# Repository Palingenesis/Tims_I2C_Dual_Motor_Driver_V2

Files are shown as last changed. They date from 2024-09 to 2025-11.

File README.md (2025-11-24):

# This is My I2C Dual Motor Driver Version 2  
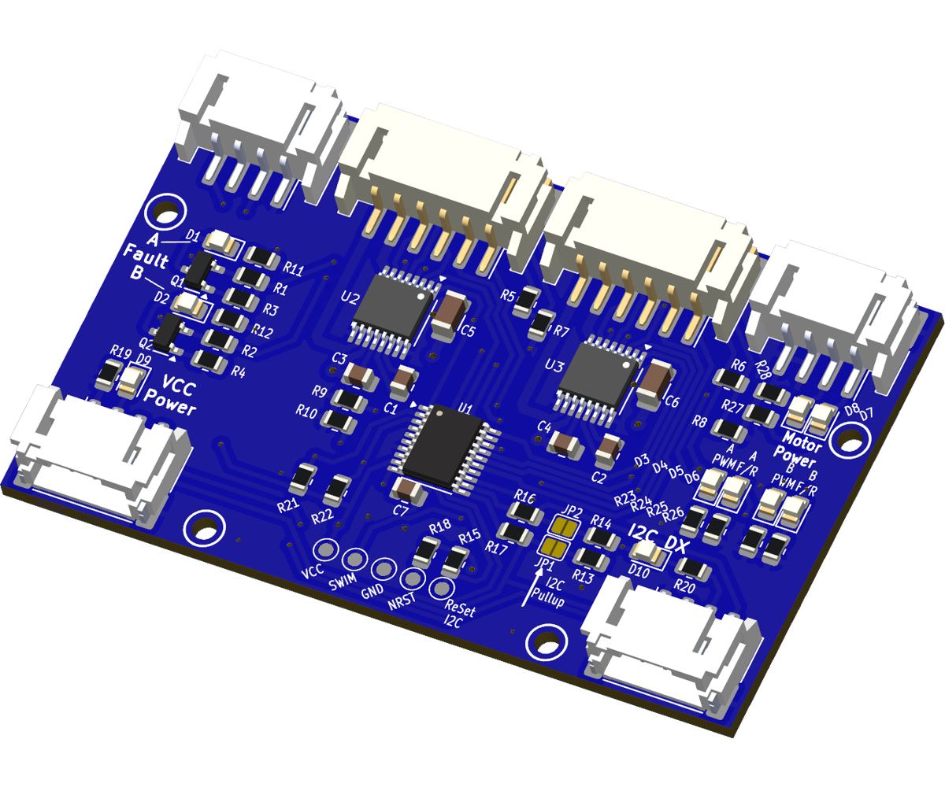
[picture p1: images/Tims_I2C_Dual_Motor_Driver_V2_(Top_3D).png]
3D Top
  
## This is an I2C controlled Dual Motor Driver Board.  
<span style="color: red; font-weight: bold;">This Board supperceeds this one [Tims I2C Dual Motor Driver](https://github.com/Palingenesis/Tims-I2C-Dual-Motor-Driver?tab=readme-ov-file)</span>
### Files are for [KiCAD EDA](https://www.kicad.org/)  
There is <span style="font-size: large;">**"Tims_I2C_Dual_Motor_Driver_V2.kicad_pcb.zip"**</span> file  
* This can be used when **"Plot Files"** asked for at 
<sub></sub> 
when ordering 10 PCBs for $5  
* If you have <span style="font-size: large;">**[KiCAD EDA](https://www.kicad.org/)**</span>,  
<sub></sub>
have a Plugin Plugin that will make things simple to order a PCB,  
just load this project into <span style="font-size: large;">**[KiCAD EDA](https://www.kicad.org/)**</span> install the plugin click the Icon Plugin and it will create all the nesesery files needed and take you to order a PCB 
and compeate the form on 
<sub></sub> 
web site.  
  
<a href="https://www.pcbway.com/project/shareproject/Tim_s_I2C_Dual_Motor_Driver_[Version_2]_0646aaaf.html">PCB from PCBWay</a>
## About  
The board can control two motors with quadratic encoders and a station to set a reference point.  
This is my second I2C Motor Driver, My first worked OK, but The MOSFETS I used where a little temperamental,  
so I decided to make a more robust version.  
This one I decided to control 2 motors from one microcontroller.  
* The main reason for having it control two motors at the same time was that I tried my original motor drivers controlling a tracked vehicle.  
It worked fine with two single motor drivers  but because I was using a web interface to control them there was a delay between turning on/off each motor.  
* I thought having a motor driver that controls two motor at the same time was a better approach.  
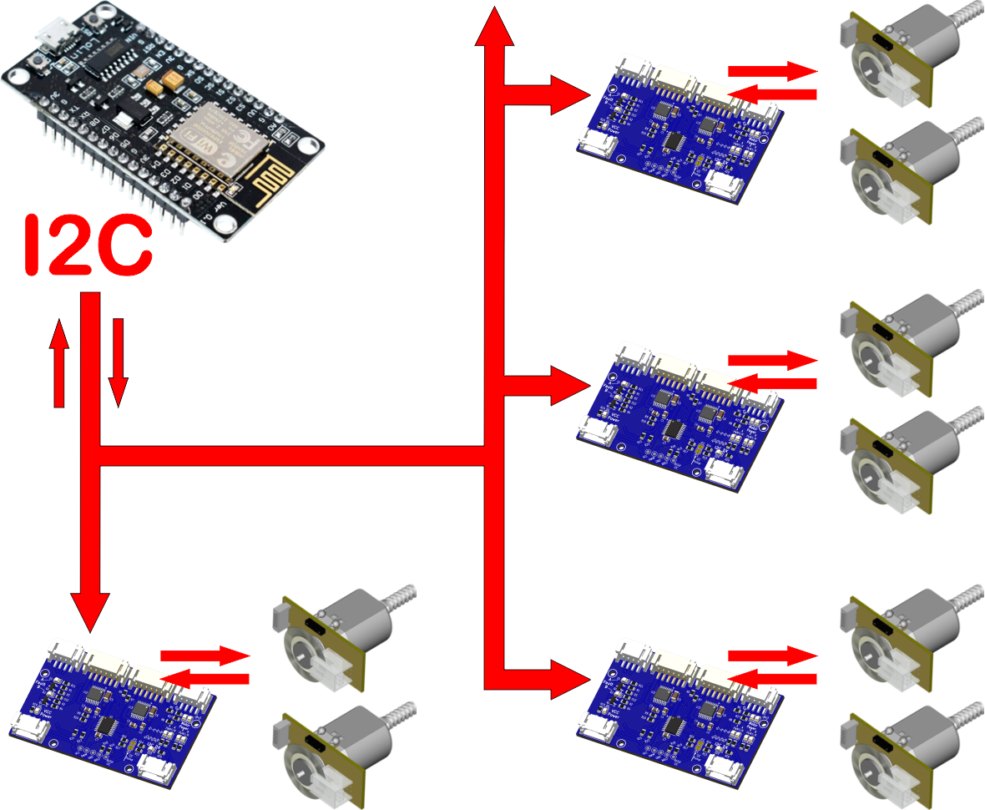
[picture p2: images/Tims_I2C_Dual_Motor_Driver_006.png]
I2C
  
## The Motor Driver is controlled via the I2C bus.  
* Each board can have its own unique I2C Address.  
* Not using the reserved Addresses over 100 in theory can be attached to one I2C bus. (Addresses 10 to 127 probably) 7-bit Address.  
* The is a system to reset the I2C default address to 0x30.  
* There are two sockets for the I2C to that the boards can be daisy-chained, end to end.  
* There is place for pull-up resistors, depending on muti-board setup or single board setup, these can be enabled/disabled.  
  
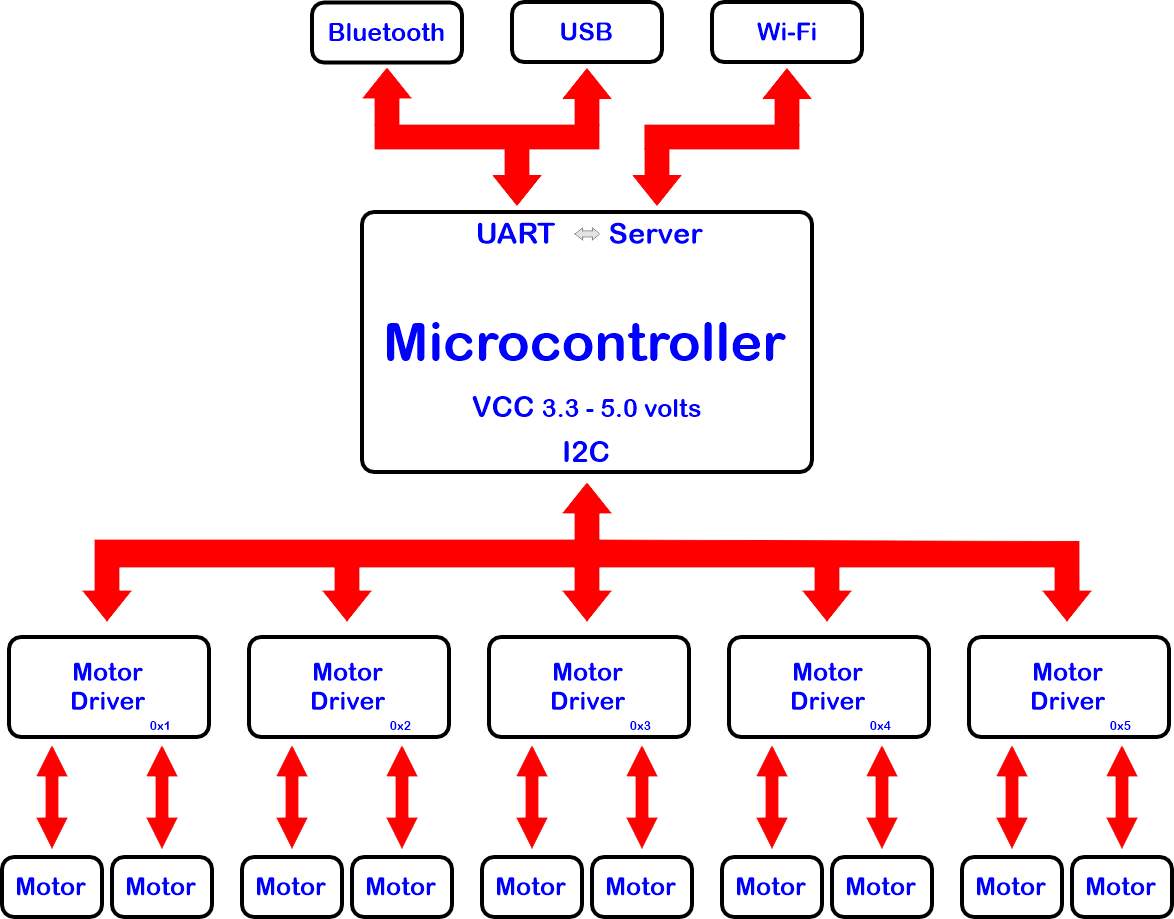
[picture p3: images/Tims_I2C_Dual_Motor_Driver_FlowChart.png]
Flow Chart
  
## The Microcontroller is the STM8S103F3
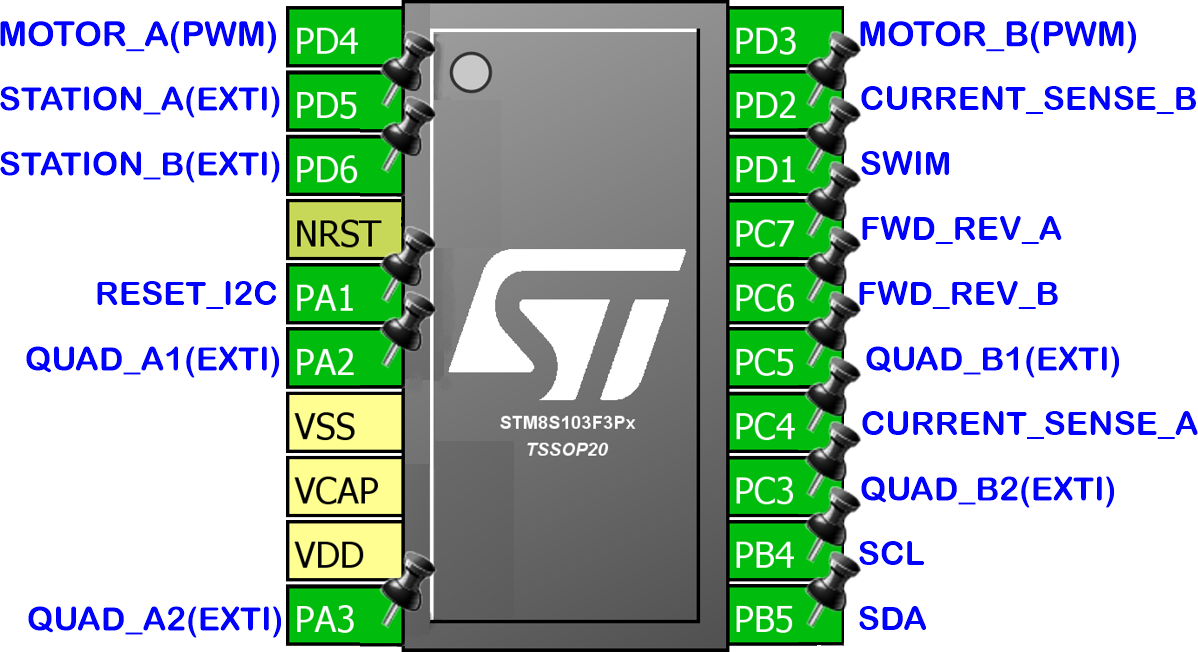
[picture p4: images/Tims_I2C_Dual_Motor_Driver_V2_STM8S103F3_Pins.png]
STM8S103F3 Pins
  
* According to the Data Sheet, this can run with 2.95 to 5.5 V operating voltage.  
* Caution should be taken when programming, The ST-Link is 3.3v.  
* I was a little limited for pins and memory, as I am controlling two motors with this. The AI has been reduced, it still has inputs for quadratic encoders and a station, these enable it to know the rotation and position of the motors.  
* I was able to use the current sense from the DRV8876, so the load on the motors can be retrieved from communication via I2C.  
## There are LEDs for diagnostics.  
* Two Yellow LEDs, one for Motor Power and one for VCC.  
* There is a red LED on the SDA line to show activity.  
* For each motor there is a red LED to show a fault, a blue LED to show Motor on and a Green LED to show if motor forward or reverse (on/off).  
## There are Pads for programming the STM8S103F3
* To program the STM8S103F3 will require STMicroelectronics "ST Visual Programmer"  
* STMicroelectronics "ST Visual Programmer" is part of "ST MCU toolset".  
* I have done .s19 file for use with the "ST Visual Programmer".  
* An ST-Link is required.
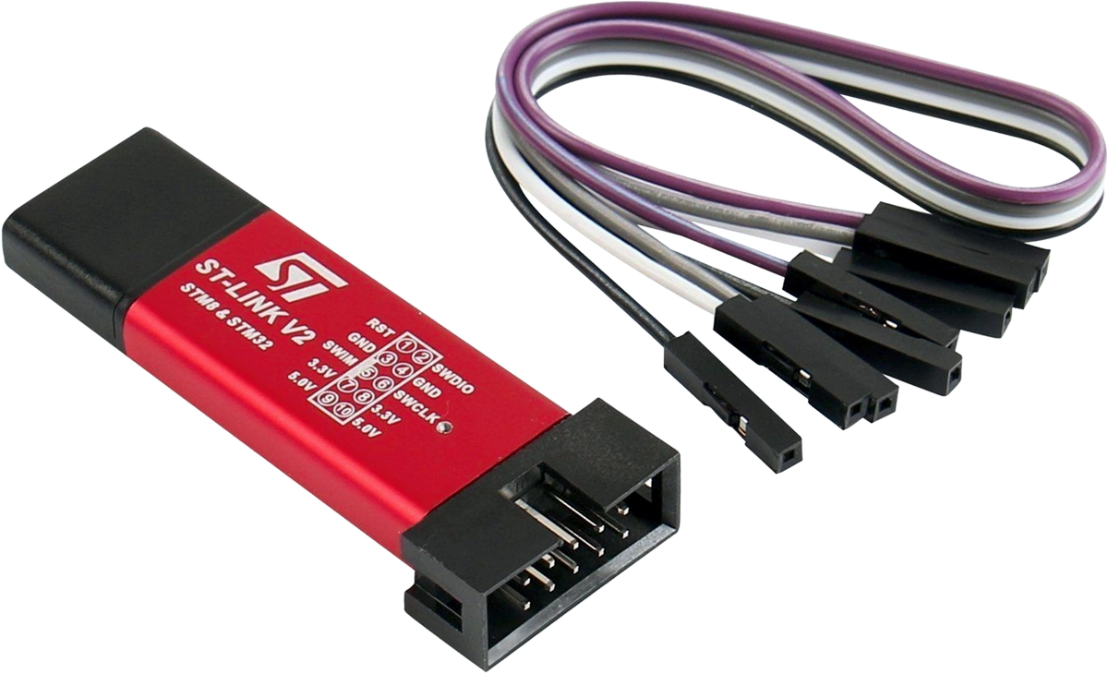
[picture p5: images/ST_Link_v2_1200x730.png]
ST-Link_v2
  
## The Drivers used are DRV8876
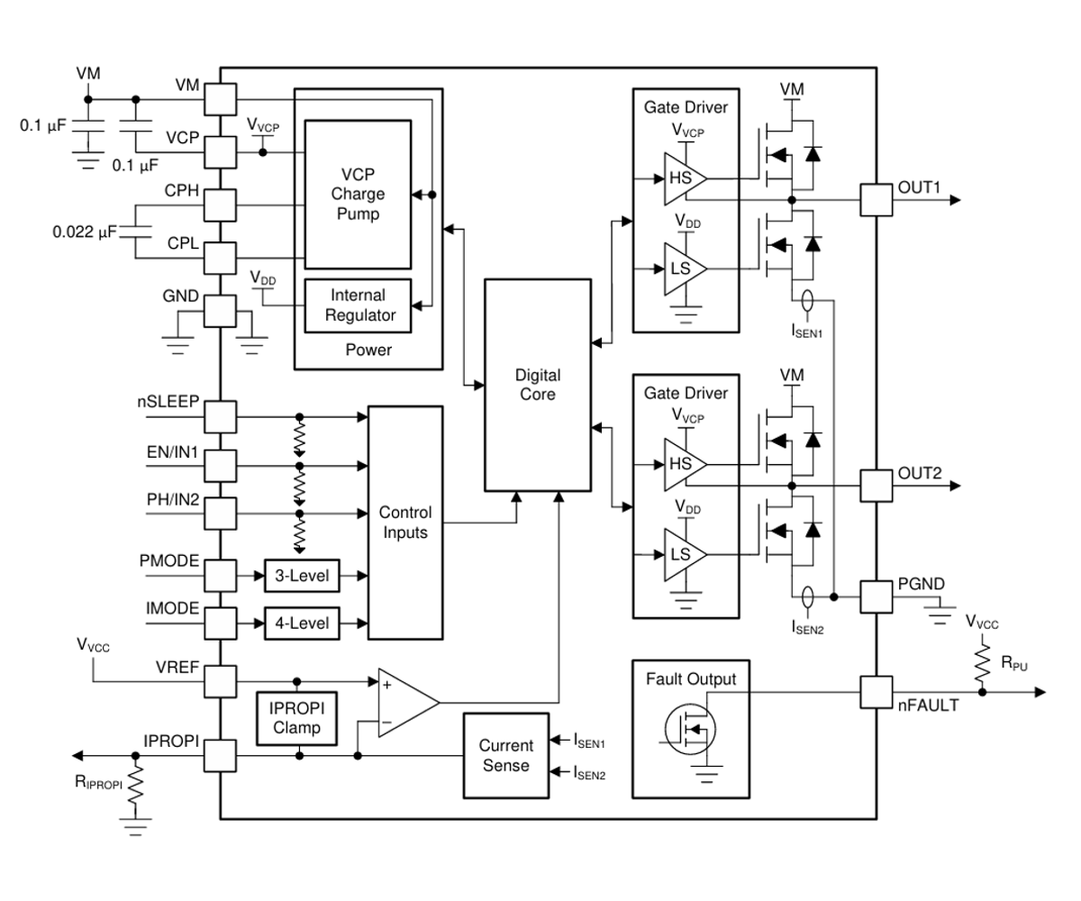
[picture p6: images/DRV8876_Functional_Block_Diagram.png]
DRV8876 Functional Block_Diagram
  
The DRV8876 is an N-channel H-bridge motor driver, the board has two of these.  
* They have 4.5-V to 37-V operating supply voltage range.  
* 3.5-A Peak. On the board I have put places for Current limit resistors.  
* Supports 1.8-V, 3.3-V, and 5-V logic inputs. (The STM8S103F3 opperates at 2.95 to 5.5 V)  
* On the board the DRV8876 are set to PH/EN Control Mode.  
* The nSleep is fixed High, so no low power mode.  
* I have connected the IPROPI to the STM8S103F3 so current readings can be sensed.  
## There are connections for a Quadratic Encoder for each Motor  
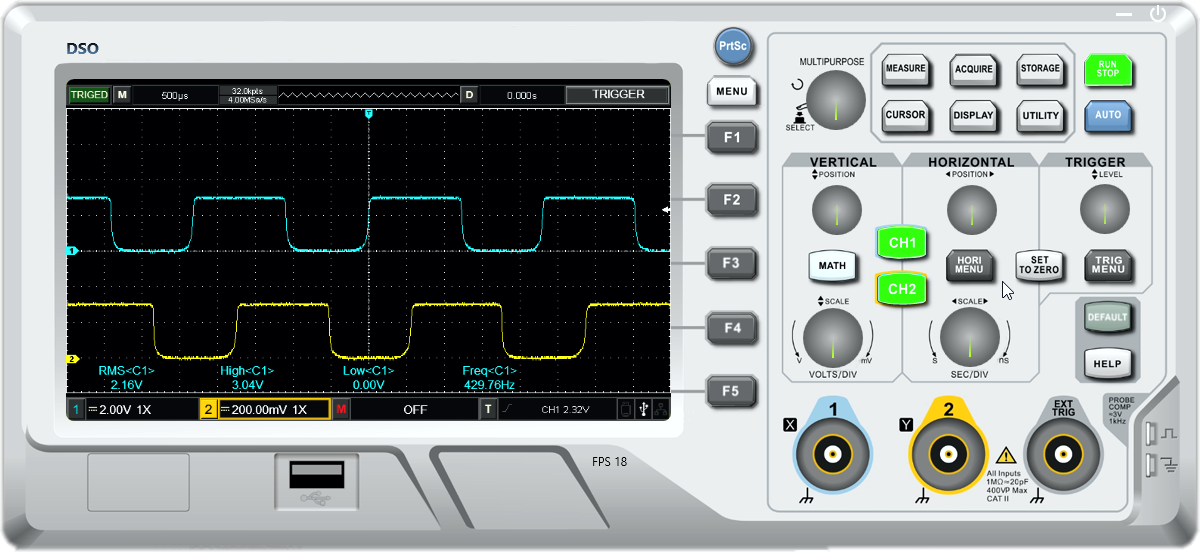
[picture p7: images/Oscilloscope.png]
Quadratic Signal
  
The Quadratic Encoder needs to be the A/B type and be the same VCC as the Board.  
* If the Board counts bacwards when the motor runs forward, the two quadratic input need to be swapped.  
* With an encoder attached to a motor, commands can be sent to set the motor to a specific position.  
## There are connections for a Station for each Motor  
* A Station is a place for a switch to be fitted to a project, that when triggerd, will reset the position of the Motor to a known position.  
* There are two settings for the station depending on the direction of the Motor, most switches don't trigger at the same point when turning on and off.  
## Commands  
The Motor Driver Board is controlled by commands on the I2C Bus.  
* The Board can be connected to any microcontroller that has I2C.  
* All commands start with any byte, this is because I have an ESP8266 and they haven't fixed the first data byte issue. When sending data via the I2C on the ESP8266 the first byte gets 0x80 added to it. So my driver ignores the first byte sent. For simplicity I will use '#' as the first character of all commands sent to the Motor Driver.  
* The second byte is the Identifier that tells the driver the type of command. All commands are from the second byte onwards. I should say "char" as all commands are sent as ASCII characters.  
## Global Command 'M'  
* **M1** = Motor A is the current motor that will be adjusted.  
* **M2** = Motor B is the current motor that will be adjusted.  
* **M3** = Motor A and B be adjusted.  
* A global command can be used on its own (preceded with '#') or at the end of other commands (preceded with a space)  
## 'C' Commands (settings):
* **C1** = Sets the Current Position to 0 (zero). Just use **C1**.  
* **C6 B\<value>** = Set: Has a Station Position. **B**oolean = 1 or 0 (true or false).  
* **C7 P\<value>** = Set the Forward Station **P**osition value. value = a 16 bit value, Sets the Station Position while moving Forward.  
* **C8 P\<value>** = Set the Reverse Station **P**osition value. value = a 16 bit value, Sets the Station Position while moving in Reverse.  
* **C10 A\<value>** = Set I2C **A**ddress. value = 1 (0x00) to 127 (0x7F). This is to change the I2C Address of the device.  
* **C13 B\<value>** = Set I2C Speed. **B**oolean; Is it 400k. value = 1 or 0 (true or false). 1 = 400000, 0 = 100000.  
All setting are saved in non volatile memory.  
* No need to apply settings every time power it connected.  
## 'S' Command (Speed):
**S\<Value>** = Set the **S**peed 0 to 1000. This is a PWM value. So 500 would be 50% on 50% off square wave.  
## 'F' Commands (Forward):
* **F0** = Stop. Can just use 'F' as the buffer will be full of zeros.  
* **F1** = Forward at a current Speed.  
* **F1 S\<value>** = Forward at a set Speed.  
## 'R' Commands (Reverse):  
* **R0** = Stop. Can just use 'R' as the buffer will be full of zeros.  
* **R1** = Reverse at a current Speed.  
* **R1** S<value> = Reverse at a set Speed.  
## 'G' Commands (Go to):
* **G0** = **Stop**. Can just use **'G'** as the buffer will be full of zeros.  
* **G1 P\<value> S\<value>** = Move to an absolute **P**osition Forward (Positive) of zero at a **S**peed.  
* **G2 P\<value> S\<value>** = Move to an absolute **P**osition Reverse (Negative) of zero at a **S**peed.  
  
*Settings that set a position are only valid with motors that have a Quadratic Encoder.*  
  
The **'G'** code **P**\<value> can be negative values. So why have **G1** and **G2**?  
* To keep options open.  
* All positions are relative to a zero.  
* When writing your own code to control the Motors you may only have the option of Unsigned Integers.  
* You may want to only use Unsigned Integers to save memory.  

### *Click this image to see a video of it in use.*
[](https://www.youtube.com/watch?v=bSmED1MQUrw)

## A Typical 4 Motor setup  
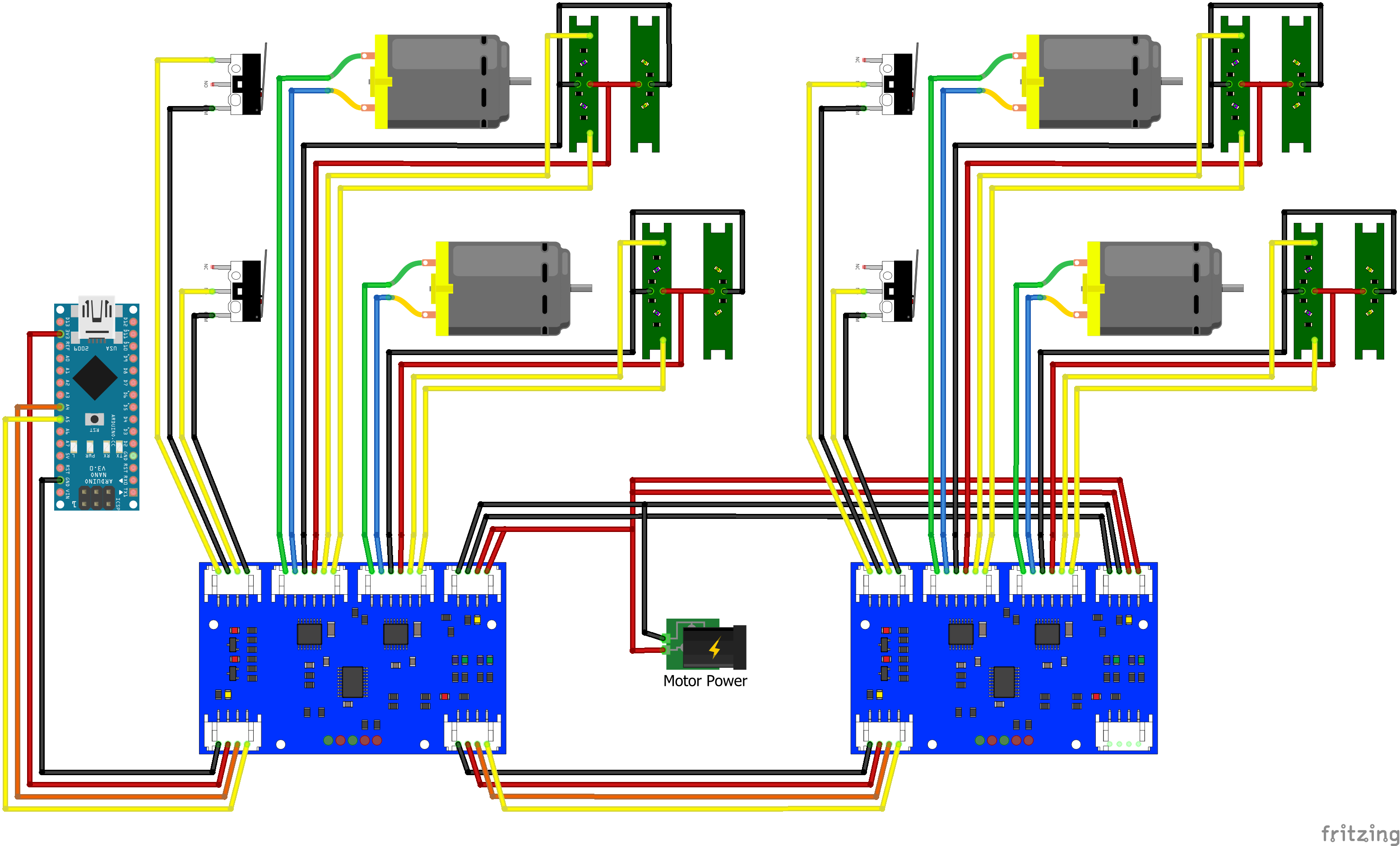
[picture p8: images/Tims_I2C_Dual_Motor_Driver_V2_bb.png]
Typical 4 Motor setup
  
* One Microcontroller.  
* Two Driver Boards.  
* Four Motors With Quadratic Encoders.  
* Each Motor has a Station to set the the zero position.  
  
  --

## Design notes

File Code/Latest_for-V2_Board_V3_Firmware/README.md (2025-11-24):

# **Changes**

This version of the driver firmware introduces several important updates:

- Added **PID control** to the `G` (Go-To) commands.  
  Motors now accelerate, cruise, and decelerate smoothly to the target position at the requested RPM.  
- Removed **current sensing** functionality.  
  The ADC code for reading motor current has been disabled to reduce FLASH needed.
- The Commands Have changed from the previous version.  
Check the "G" commands.  
No forward reverse "F", "R", replaced with "B" Basic.

---

## Command Overview

The firmware supports a set of commands, each identified by a single letter.  
My rule of thumb for letter assignments is:

- **A** → Address (I²C related)  
- **B** → Basic Movement (direct PWM control)  
- **C** → Change Setting (configuration)  
- **F** → Flag (true/false values)  
- **G** → Go-To Movement (PID controlled position moves)  
- **M** → Motor selection (A, B, or both)  
- **N** → Number (encoder counts, etc.)  
- **P** → Position (absolute target position)  
- **R** → Rate (acceleration/deceleration)  
- **S** → Speed (RPM in Go-To mode, PWM in Basic mode)  

---

## Command Details

### `B` — Basic Movement
- `B0` → Stop motor  
- `B1` → Forward  
- `B2` → Reverse  
- Speed is set with `S` (0–1000 = PWM duty cycle)

### `G` — Go-To Movement
- `G00` → Stop  
- `G01 P<value> S<value>` → Move to absolute position at given speed (RPM)  
- Example: `G01 P1000 S50 M1` → Move Motor A to position 1000 at 50 RPM

### `C` — Change Settings
- `C0` → Reset positions to zero  
- `C1 P<value>` → Set current position  
- `C6 F<value>` → Enable/disable station flag  
- `C7 P<value>` → Set forward station position  
- `C8 P<value>` → Set reverse station position  
- `C10 A<value>` → Change I²C address  
- `C13 F<value>` → Set I²C speed (100k/400k)  
- `C14 R<value>` → Set acceleration rate  
- `C15 N<value>` → Set encoder count  

### `S` — Speed
- In **Basic mode (`B`)**: 0–1000 = PWM duty cycle  
- In **Go-To mode (`G`)**: 0–1000 = RPM  

### `M` — Motor Selection
- `M1` → Motor A  
- `M2` → Motor B  
- `M3` → Both motors  

---
## Example Commands

### **'G' Command**
- `G01 P2000 S500 M1\r\n`  
  Move **Motor A** to **Position 2000** at **500 RPM**.  
  *Note: `P` (Position) can be a negative **int32_t** value.*
  
### **'B' Command**
- `B1 S750 M2\r\n`  
  Run **Motor B** forward at **75% PWM duty cycle**.  
- `B0 M3\r\n`  
  Stop **Motors A and B**.

---

## Notes on Command Transmission

All commands should:
- Be sent to the I²C address defined in **Settings**.
- **End** with `\r\n`.
- **A garbage Char should be sent befor the command**
- `#` (or any single character — it is ignored due to an ESP8266 I²C bug).  

### Example: Sending a Command Buffer

```c
int Target_I2C_Address = 0x30;
char Buffer_TX[BUFF_64];    /* message */

void SendBufferOnI2C(int I2C_address) {
    Wire.beginTransmission(I2C_address);   // Get device at I2C_address attention
    Wire.write('#');                       /* Send garbage for the first byte (ignored) */
    Wire.write(Buffer_TX, sofar);          // Send Buffer_TX
    Wire.endTransmission();                // Stop transmitting
}

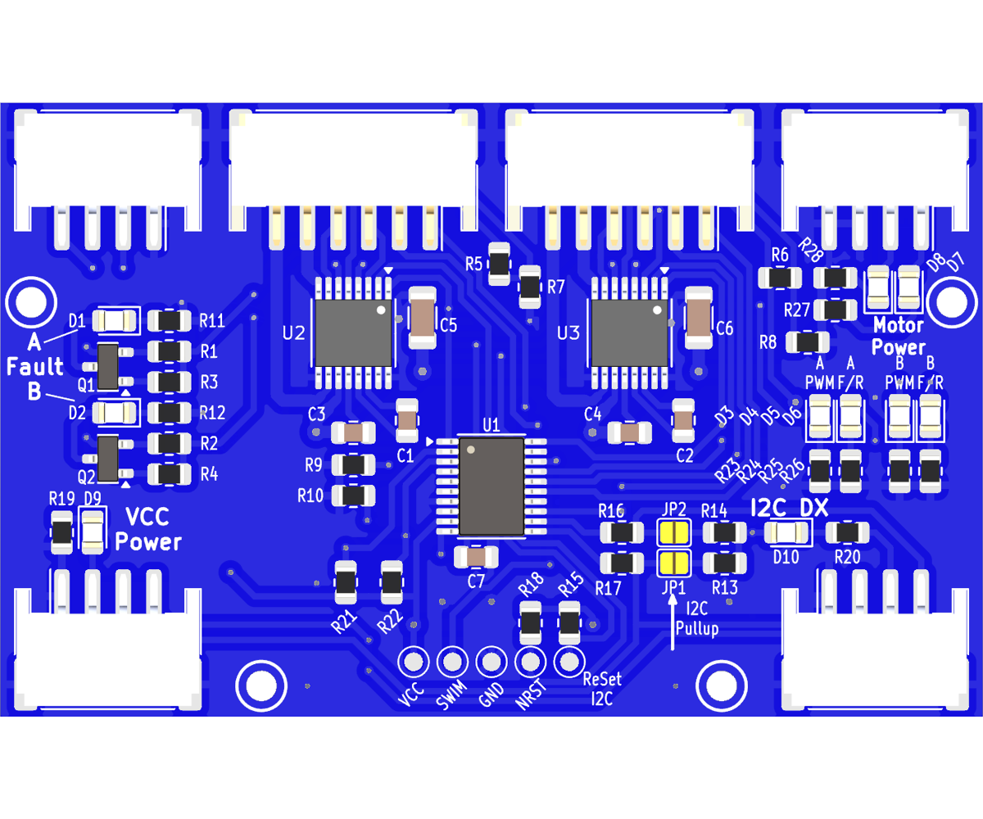
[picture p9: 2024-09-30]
images/Tims_I2C_Dual_Motor_Driver_V2 (Top).png

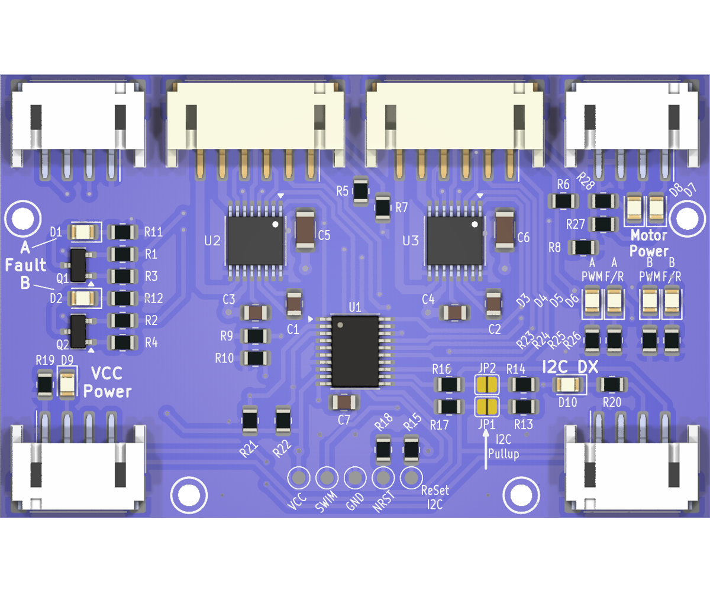
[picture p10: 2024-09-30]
images/Tims_I2C_Dual_Motor_Driver_V2 (Ren Top).png

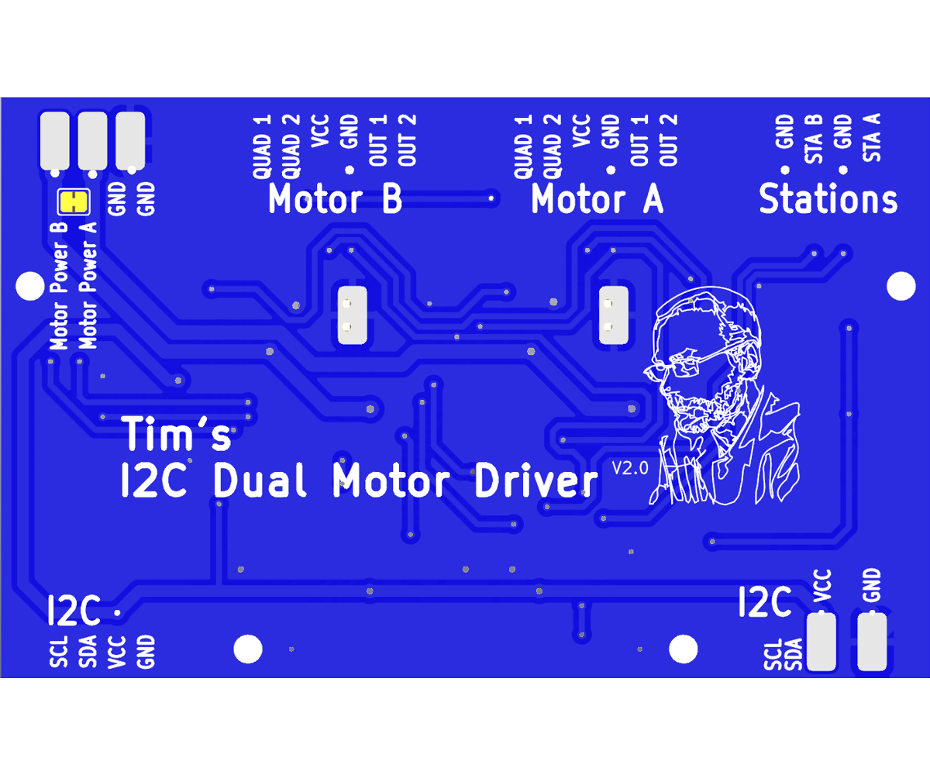
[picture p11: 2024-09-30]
images/Tims_I2C_Dual_Motor_Driver_V2 (Bottom).png

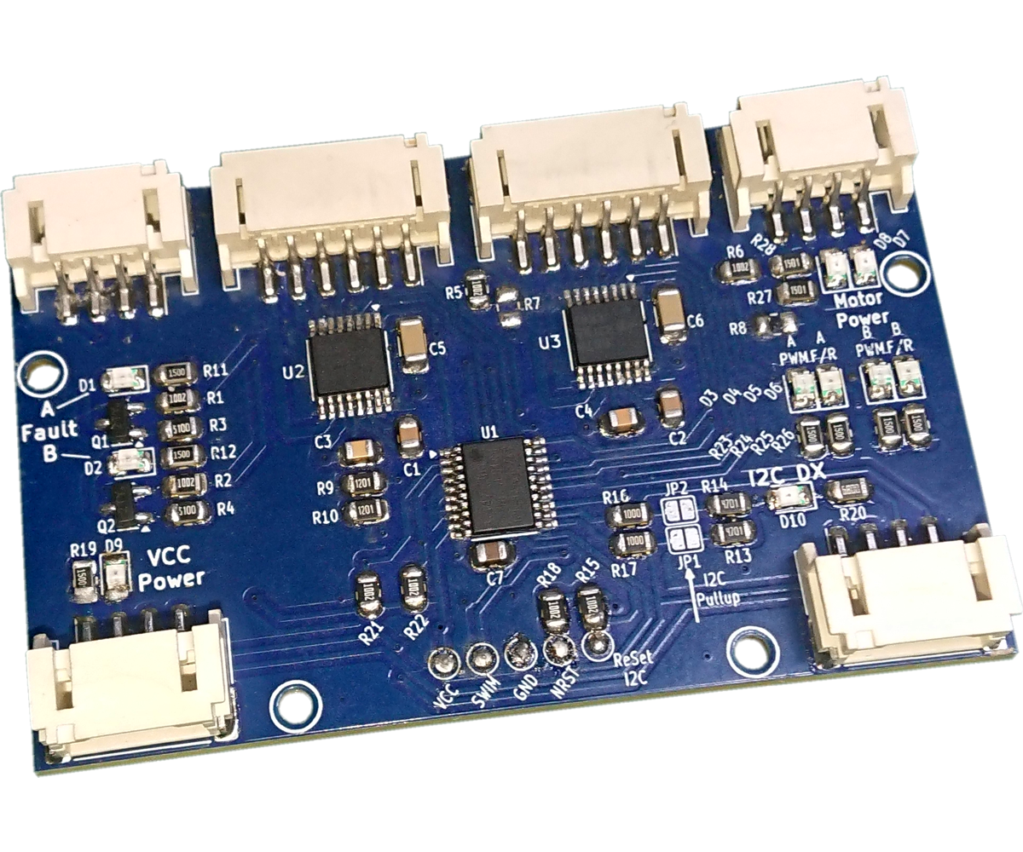
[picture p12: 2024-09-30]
images/Tims_I2C_Dual_Motor_Driver_V2_I2C.png

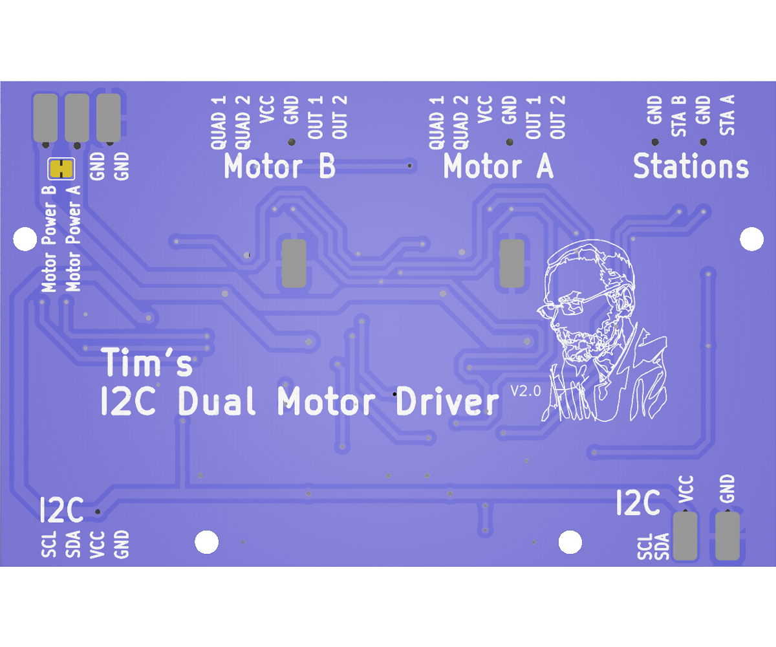
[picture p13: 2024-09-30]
images/Tims_I2C_Dual_Motor_Driver_V2 (Ren Bottom).png

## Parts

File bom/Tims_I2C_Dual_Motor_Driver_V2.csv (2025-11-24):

null | Sourced | Placed | References | Value | Footprint | Sourced From | Datasheet | Description | Quantity
1 | ✓ | ✓ | C1, C2 | 22nF | C_0805_2012Metric |  |  | Unpolarized capacitor | 2
2 | ✓ | ✓ | C3, C4 | 100nF | C_0805_2012Metric |  |  | Unpolarized capacitor | 2
3 | ✓ | ✓ | C5, C6 | 100nF | C_1206_3216Metric |  |  | Unpolarized capacitor | 2
4 | ✓ | ✓ | C7 | 1uF | C_0805_2012Metric |  |  | Unpolarized capacitor | 1
5 | ✓ | ✓ | R1, R2, R5, R6, R15, R18, R21, R22 | 10k | R_0805_2012Metric |  |  | Resistor | 8
6 | ✓ | ✓ | R11, R12, R19, R23, R24, R25, R26 | 150R | R_0805_2012Metric |  |  | Resistor | 7
7 | ✓ | ✓ | R3, R4 | 510R | R_0805_2012Metric |  |  | Resistor | 2
8 | ✓ | ✓ | R7, R8 | Omit | R_0805_2012Metric |  |  | Resistor | 2
9 | ✓ | ✓ | R9, R10 | 1k3 | R_0805_2012Metric |  |  | Resistor | 2
10 | ✓ | ✓ | R13, R14 | 4k7 | R_0805_2012Metric |  |  | Resistor | 2
11 | ✓ | ✓ | R16, R17 | 100R | R_0805_2012Metric |  |  | Resistor | 2
12 | ✓ | ✓ | R27, R28 | 1K5 | R_0805_2012Metric |  |  | Resistor | 2
13 | ✓ | ✓ | R20 | 680R | R_0805_2012Metric |  |  | Resistor | 1
14 | ✓ | ✓ | D1, D2, D10 | LED (Red) | LED_0805_2012Metric |  |  | Light emitting diode | 3
15 | ✓ | ✓ | D7, D8, D9 | LED (Yellow) | LED_0805_2012Metric |  |  | Light emitting diode | 3
16 | ✓ | ✓ | D3, D5 | LED (Blue) | LED_0805_2012Metric |  |  | Light emitting diode | 2
17 | ✓ | ✓ | D4, D6 | LED (Green) | LED_0805_2012Metric |  |  | Light emitting diode | 2
18 | ✓ | ✓ | U2, U3 | DRV8876 | HTSSOP-16-1EP_4.4x5mm_P0.65mm_EP3x3mm | https://www.digikey.co.uk/en/products/detail/texas-instruments/DRV8876PWPR/10270191 | https://www.ti.com/lit/ds/symlink/drv8876.pdf?ts=1717632359923 | H-Bridge driver, 3.5A, Low Voltage, PH/EN input | 2
19 | ✓ | ✓ | U1 | STM8S103F | TSSOP-20_4.4x6.5mm_P0.65mm |  | http://www.st.com/st-web-ui/static/active/en/resource/technical/document/datasheet/DM00024550.pdf | 16MHz, 8K Flash, 1K RAM, 128 EEPROM, USART, I²C, SPI, TSSOP-20 | 1
20 | ✓ | ✓ | Q1, Q2 | PNP_S8550 | SOT-23 |  |  | PNP transistor, base/emitter/collector | 2
21 | ✓ | ✓ | J1, J2 | I2C | JST_PH_S4B-PH-SM4-TB_1x04-1MP_P2.00mm_Horizontal |  | https://www.jst-mfg.com/product/pdf/eng/ePH.pdf | Generic connectable mounting pin connector, single row, 01x04, script generated (kicad-library-utils/schlib/autogen/connector/) | 2
22 | ✓ | ✓ | J3 | Stations | JST_PH_S4B-PH-SM4-TB_1x04-1MP_P2.00mm_Horizontal |  | https://www.jst-mfg.com/product/pdf/eng/ePH.pdf | Generic connectable mounting pin connector, single row, 01x04, script generated (kicad-library-utils/schlib/autogen/connector/) | 1
23 | ✓ | ✓ | J4 | Motor A | JST_PH_S6B-PH-SM4-TB_1x06-1MP_P2.00mm_Horizontal | https://www.digikey.co.uk/en/products/detail/jst-sales-america-inc/S8B-PH-SM4-TB/926661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 | https://www.jst-mfg.com/product/pdf/eng/ePH.pdf | Generic connectable mounting pin connector, single row, 01x06, script generated (kicad-library-utils/schlib/autogen/connector/) | 1
24 | ✓ | ✓ | J5 | Motor B | JST_PH_S6B-PH-SM4-TB_1x06-1MP_P2.00mm_Horizontal | https://www.digikey.co.uk/en/products/detail/jst-sales-america-inc/S8B-PH-SM4-TB/926661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 | https://www.jst-mfg.com/product/pdf/eng/ePH.pdf | Generic connectable mounting pin connector, single row, 01x06, script generated (kicad-library-utils/schlib/autogen/connector/) | 1
25 | ✓ | ✓ | J6 | Motor Power | JST_PH_S4B-PH-SM4-TB_1x04-1MP_P2.00mm_Horizontal |  | https://www.jst-mfg.com/product/pdf/eng/ePH.pdf | Generic connectable mounting pin connector, single row, 01x04, script generated (kicad-library-utils/schlib/autogen/connector/) | 1

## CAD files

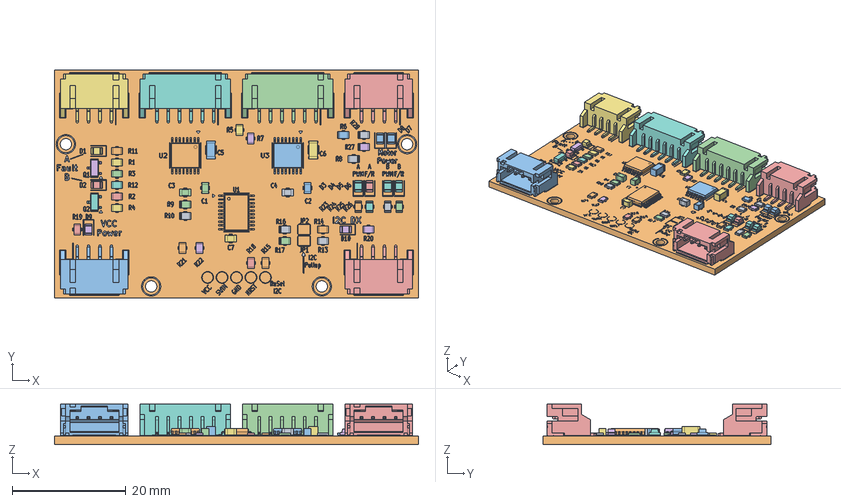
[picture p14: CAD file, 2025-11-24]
Tims_I2C_Dual_Motor_Driver_V2.FCStd
64.0 x 40.0 x 7.17 mm
R_0805_2012Metric
DRV8876PWPR
C_0805_2012Metric
R_0805_2012Metric001
LED_0805_2012Metric
LED_0805_2012Metric001
C_0805_2012Metric001
LED_0805_2012Metric002
R_0805_2012Metric002
R_0805_2012Metric003
SxB-PH-SM4-TB white_4
C_0805_2012Metric002
R_0805_2012Metric004
LED_0805_2012Metric003
R_0805_2012Metric005
LED_0805_2012Metric004
R_0805_2012Metric006
TSSOP-20_4.4x6.5mm_P0.65mm
R_0805_2012Metric007
S6B-PH-SM4-TB
SxB-PH-SM4-TB white_005
R_0805_2012Metric008
LED_0805_2012Metric005
R_0805_2012Metric009
C_0805_2012Metric003
R_0805_2012Metric010
C_1206_3216Metric
R_0805_2012Metric011
LED_0805_2012Metric006
SOT-23
C_1206_3216Metric001
R_0805_2012Metric012
R_0805_2012Metric013
R_0805_2012Metric014
DRV8876PWPR001
R_0805_2012Metric015
R_0805_2012Metric016
R_0805_2012Metric017
SxB-PH-SM4-TB white_006
SOT-024
R_0805_2012Metric018
R_0805_2012Metric019
LED_0805_2012Metric007
C_0805_2012Metric004
SxB-PH-SM4-TB white_007
R_0805_2012Metric020
R_0805_2012Metric021
LED_0805_2012Metric008
R_0805_2012Metric022
R_0805_2012Metric023
LED_0805_2012Metric009
R_0805_2012Metric024
R_0805_2012Metric025
R_0805_2012Metric026
R_0805_2012Metric027
S6B-PH-SM4-TB001
Tims_I2C_Dual_Motor_Driver_V2_silkscreen
Tims_I2C_Dual_Motor_Driver_V2_PCB

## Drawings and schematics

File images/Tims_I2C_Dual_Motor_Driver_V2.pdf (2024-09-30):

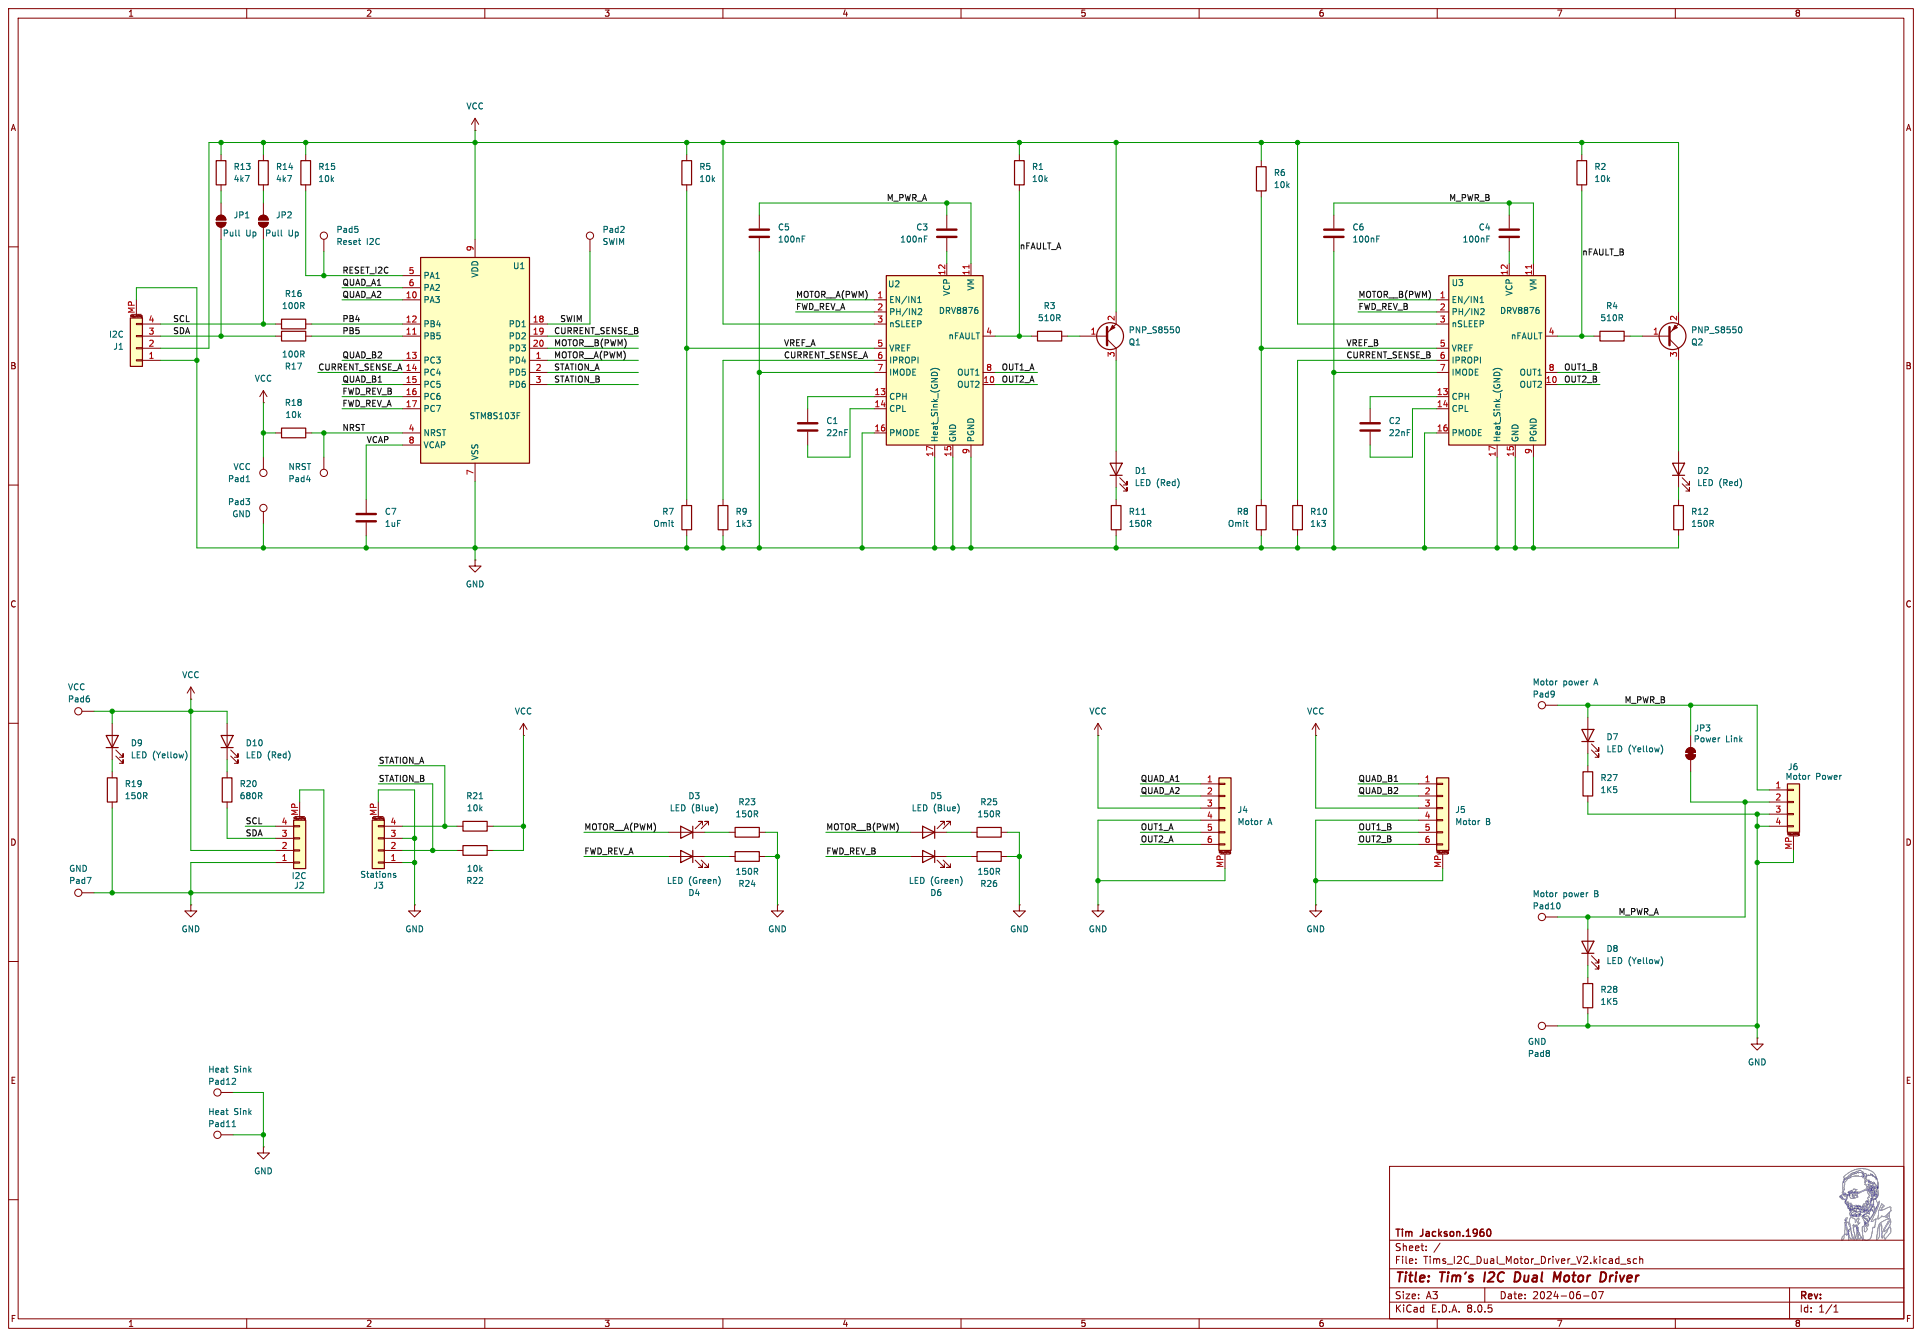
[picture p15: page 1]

LED (Yellow) Pad9 Motor power A D10

Id: 1/1 Title: Tim's I2C Dual Motor Driver File: Tims_I2C_Dual_Motor_Driver_V2.kicad_sch Sheet: / Tim Jackson.1960

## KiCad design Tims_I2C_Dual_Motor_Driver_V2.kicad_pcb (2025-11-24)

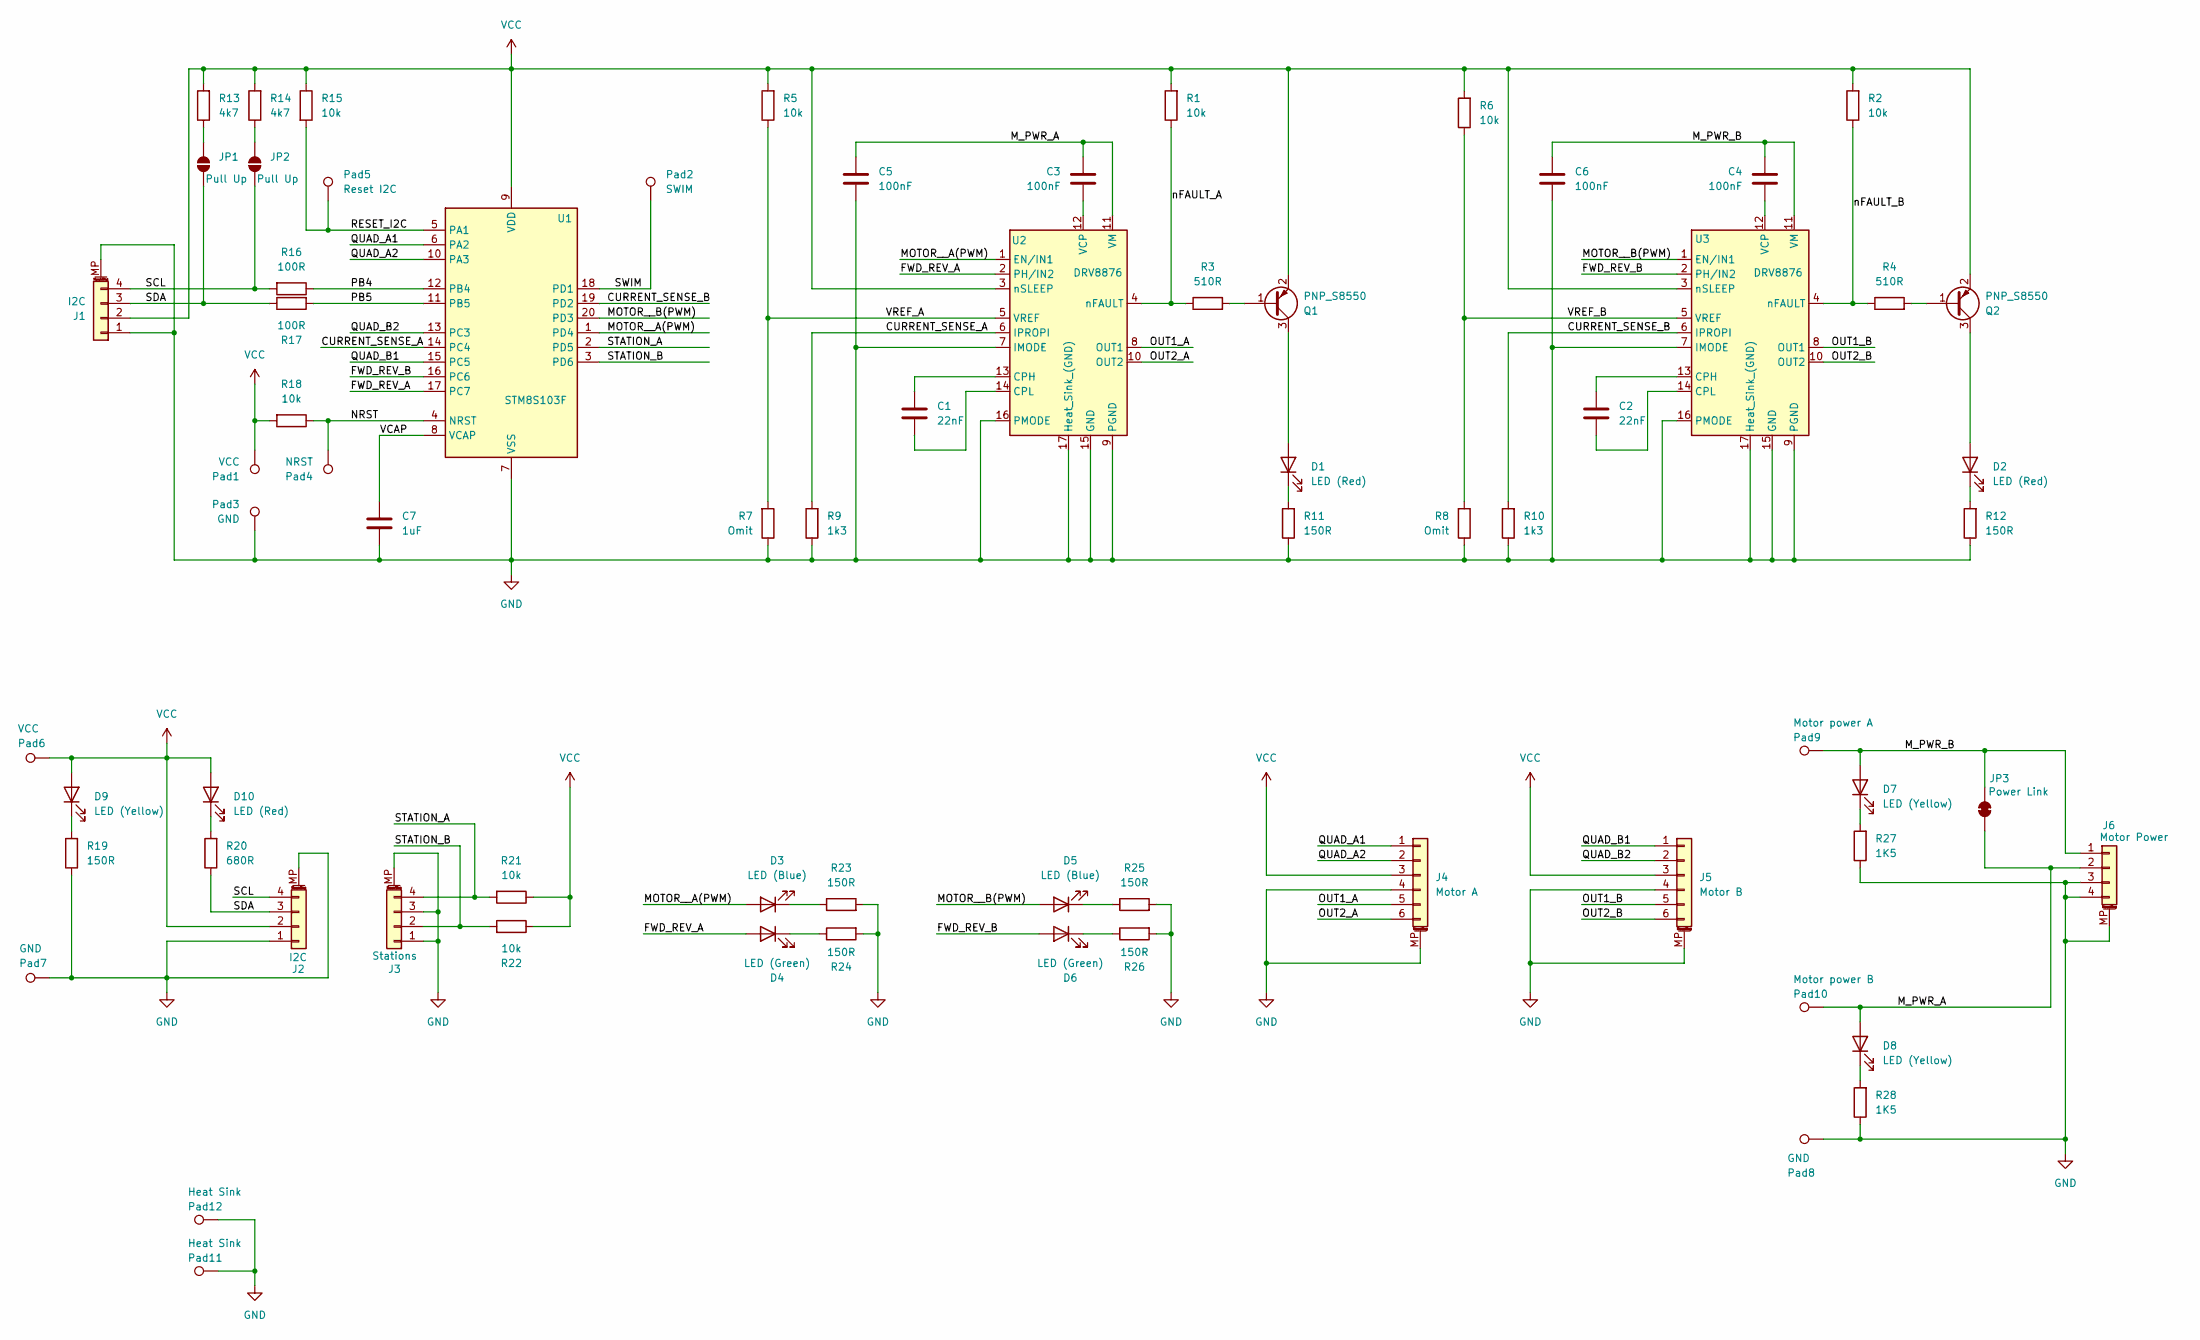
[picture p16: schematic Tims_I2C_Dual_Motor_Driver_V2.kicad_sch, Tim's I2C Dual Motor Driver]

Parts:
C1, C2: 22nF; C_0805_2012Metric
C3, C4: 100nF; C_0805_2012Metric
C5, C6: 100nF; C_1206_3216Metric
C7: 1uF; C_0805_2012Metric
D1, D2, D10: LED (Red); LED_0805_2012Metric
D3, D5: LED (Blue); LED_0805_2012Metric
D4, D6: LED (Green); LED_0805_2012Metric
D7, D8, D9: LED (Yellow); LED_0805_2012Metric
J1, J2: I2C; JST_PH_S4B-PH-SM4-TB_1x04-1MP_P2.00mm_Horizontal
J3: Stations; JST_PH_S4B-PH-SM4-TB_1x04-1MP_P2.00mm_Horizontal
J4: Motor A; JST_PH_S6B-PH-SM4-TB_1x06-1MP_P2.00mm_Horizontal
J5: Motor B; JST_PH_S6B-PH-SM4-TB_1x06-1MP_P2.00mm_Horizontal
J6: Motor Power; JST_PH_S4B-PH-SM4-TB_1x04-1MP_P2.00mm_Horizontal
JP1, JP2: Pull Up; SolderJumper-2_P1.3mm_Open_RoundedPad1.0x1.0mm
JP3: Power Link; SolderJumper-2_P1.3mm_Bridged_RoundedPad1.0x1.0mm
Pad1, Pad6: VCC; Wire_Conn
Pad2: SWIM; Wire_Conn
Pad3, Pad7, Pad8: GND; Wire_Conn
Pad4: NRST; Wire_Conn
Pad5: Reset I2C; Wire_Conn
Pad9: Motor power A; Wire_Conn
Pad10: Motor power B; Wire_Conn
Pad11, Pad12: Heat Sink; Wire_Conn
Q1, Q2: PNP_S8550; SOT-23
R1, R2, R5, R6, R15, R18, R21, R22: 10k; R_0805_2012Metric
R3, R4: 510R; R_0805_2012Metric
R7, R8: Omit; R_0805_2012Metric
R9, R10: 1k3; R_0805_2012Metric
R11, R12, R19, R23, R24, R25, R26: 150R; R_0805_2012Metric
R13, R14: 4k7; R_0805_2012Metric
R16, R17: 100R; R_0805_2012Metric
R20: 680R; R_0805_2012Metric
R27, R28: 1K5; R_0805_2012Metric
U1: STM8S103F; TSSOP-20_4.4x6.5mm_P0.65mm
U2, U3: DRV8876; HTSSOP-16-1EP_4.4x5mm_P0.65mm_EP3x3mm

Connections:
/CURRENT_SENSE_A: R9.2, U1.14 (PC4), U2.6 (IPROPI)
/CURRENT_SENSE_B: R10.2, U1.19 (PD2), U3.6 (IPROPI)
/FWD_REV_A: D4.2 (A), U1.17 (PC7), U2.2 (PH/IN2)
/FWD_REV_B: D6.2 (A), U1.16 (PC6), U3.2 (PH/IN2)
/MOTOR__A(PWM): D3.2 (A), U1.1 (PD4), U2.1 (EN/IN1)
/MOTOR__B(PWM): D5.2 (A), U1.20 (PD3), U3.1 (EN/IN1)
/M_PWR_A: C3.2, C5.1, D8.2 (A), J6.2, JP3.1 (A), Pad10.1, U2.11 (VM)
/M_PWR_B: C4.2, C6.1, D7.2 (A), J6.1, JP3.2 (B), Pad9.1, U3.11 (VM)
/NRST: Pad4.1, R18.1, U1.4 (NRST)
/OUT1_A: J4.5, U2.8 (OUT1)
/OUT1_B: J5.5, U3.8 (OUT1)
/OUT2_A: J4.6, U2.10 (OUT2)
/OUT2_B: J5.6, U3.10 (OUT2)
/PB4: R16.1, U1.12 (PB4)
/PB5: R17.2, U1.11 (PB5)
/QUAD_A1: J4.1, U1.6 (PA2)
/QUAD_A2: J4.2, U1.10 (PA3)
/QUAD_B1: J5.1, U1.15 (PC5)
/QUAD_B2: J5.2, U1.13 (PC3)
/RESET_I2C: Pad5.1, R15.2, U1.5 (PA1)
/SCL: J1.4, J2.4, JP2.1 (A), R16.2
/SDA: J1.3, J2.3, JP1.1 (A), R17.1, R20.1
/STATION_A: J3.4, R21.2, U1.2 (PD5)
/STATION_B: J3.2, R22.2, U1.3 (PD6)
/SWIM: Pad2.1, U1.18 (PD1)
/VCAP: C7.1, U1.8 (VCAP)
/VREF_A: R5.1, R7.2, U2.5 (VREF)
/VREF_B: R6.1, R8.2, U3.5 (VREF)
/nFAULT_A: R1.1, R3.1, U2.4 (nFAULT)
/nFAULT_B: R2.1, R4.1, U3.4 (nFAULT)
GND: C5.2, C6.2, C7.2, J1.1, J1.MP (MountPin), J2.1, J2.MP (MountPin), J3.1, J3.3, J3.MP (MountPin), J4.4, J4.MP (MountPin), J5.4, J5.MP (MountPin), J6.3, J6.4, J6.MP (MountPin), Pad3.1, Pad7.1, Pad8.1, Pad11.1, Pad12.1, R7.1, R8.1, R9.1, R10.1, R11.1, R12.1, R19.1, R23.2, R24.2, R25.2, R26.2, R27.1, R28.1, U1.7 (VSS), U2.7 (IMODE), U2.9 (PGND), U2.15 (GND), U2.16 (PMODE), U2.17 (Heat_Sink_(GND)), U3.7 (IMODE), U3.9 (PGND), U3.15 (GND), U3.16 (PMODE), U3.17 (Heat_Sink_(GND))
unnamed: D1.2 (A), Q1.3 (C)
unnamed: D1.1 (K), R11.2
unnamed: D2.2 (A), Q2.3 (C)
unnamed: D2.1 (K), R12.2
unnamed: D3.1 (K), R23.1
unnamed: D4.1 (K), R24.1
unnamed: D5.1 (K), R25.1
unnamed: D6.1 (K), R26.1
unnamed: D7.1 (K), R27.2
unnamed: D8.1 (K), R28.2
unnamed: D9.1 (K), R19.2
unnamed: D10.1 (K), R20.2
unnamed: JP1.2 (B), R13.1
unnamed: JP2.2 (B), R14.1
unnamed: Q1.1 (B), R3.2
unnamed: Q2.1 (B), R4.2
unnamed: C1.1, U2.13 (CPH)
unnamed: C1.2, U2.14 (CPL)
unnamed: C3.1, U2.12 (VCP)
unnamed: C2.1, U3.13 (CPH)
unnamed: C2.2, U3.14 (CPL)
unnamed: C4.1, U3.12 (VCP)
VCC: D9.2 (A), D10.2 (A), J1.2, J2.2, J4.3, J5.3, Pad1.1, Pad6.1, Q1.2 (E), Q2.2 (E), R1.2, R2.2, R5.2, R6.2, R13.2, R14.2, R15.1, R18.2, R21.1, R22.1, U1.9 (VDD), U2.3 (nSLEEP), U3.3 (nSLEEP)

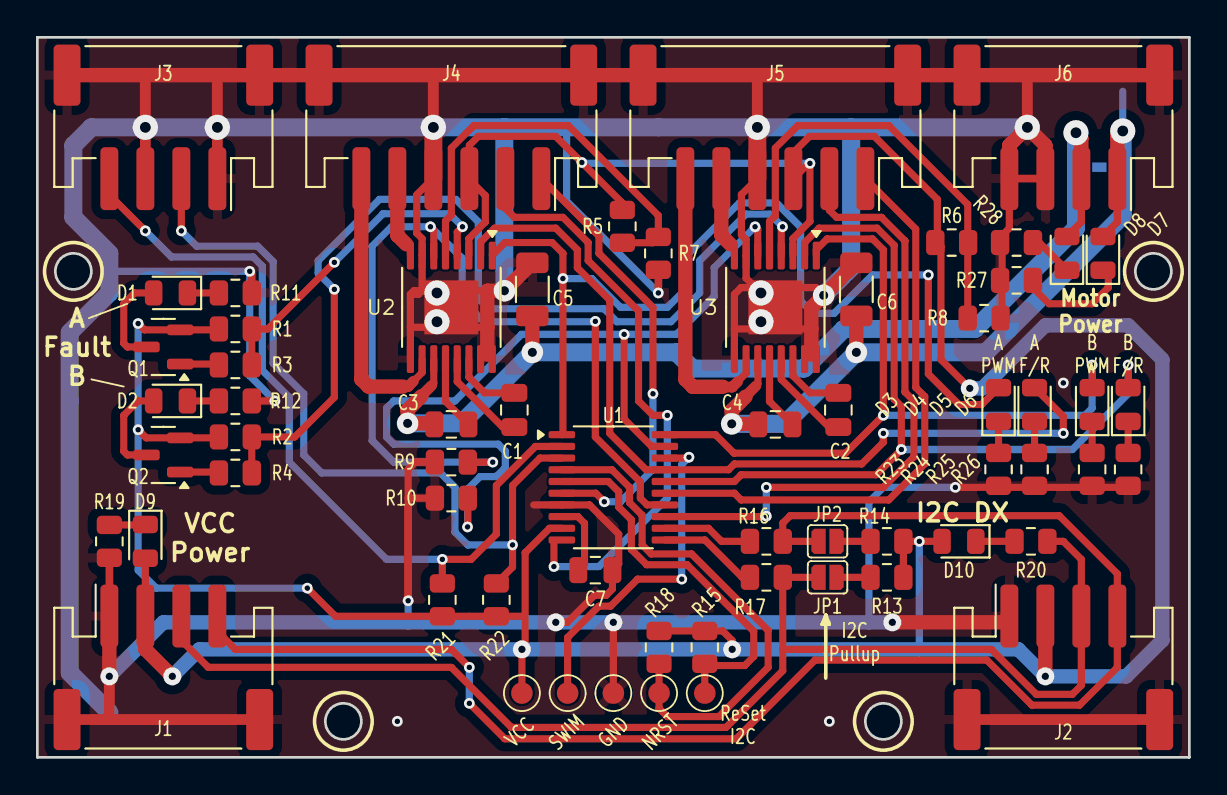
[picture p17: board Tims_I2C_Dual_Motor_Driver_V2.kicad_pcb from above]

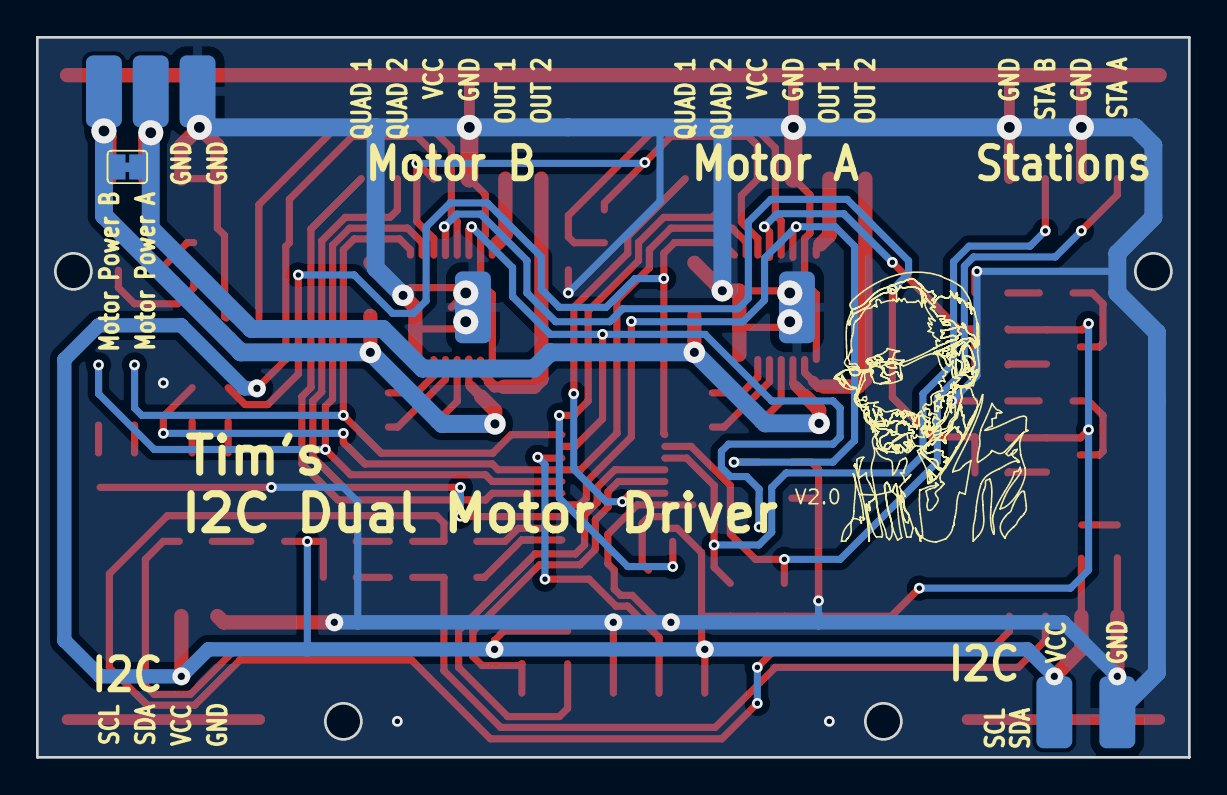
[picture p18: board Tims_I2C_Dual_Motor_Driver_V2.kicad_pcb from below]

Board: 2 copper layers, 64.0 x 40.0 mm, 71 parts (8 on the bottom side), 54 nets.

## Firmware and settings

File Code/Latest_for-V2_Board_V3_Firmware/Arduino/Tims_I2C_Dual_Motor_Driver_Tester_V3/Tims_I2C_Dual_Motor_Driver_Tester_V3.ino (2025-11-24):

/*
	A small program to send commands via Serial to Tim's I2C Dual Motor Driver V3.

	By Tim Jackson.1960
		More info on Instructables. https://www.instructables.com/member/Palingenesis/instructables/


	ESP8266 (2M SPIFFS)
		Variables and constants in RAM (global, static), used 29504 / 80192 bytes (36%)
			SEGMENT  BYTES    DESCRIPTION
			DATA     1516     initialized variables
			RODATA   1364     constants
			BSS      26624    zeroed variables
		Instruction RAM (IRAM_ATTR, ICACHE_RAM_ATTR), used 62223 / 65536 bytes (94%)
			SEGMENT  BYTES    DESCRIPTION
			ICACHE   32768    reserved space for flash instruction cache
			IRAM     29455    code in IRAM
		Code in flash (default, ICACHE_FLASH_ATTR), used 243028 / 1048576 bytes (23%)
			SEGMENT  BYTES    DESCRIPTION
			IROM     243028   code in flash

	Arduino NANO ATMega328p
		Sketch uses 8628 bytes (28%) of program storage space. Maximum is 30720 bytes.
		Global variables use 968 bytes (47%) of dynamic memory, leaving 1080 bytes for local variables. Maximum is 2048 bytes.


	Wire request buffer of the Motor Driver was originaly set/configured for 32 bit values but was reduced to 24+ bit numbers.
	The original code is commented out should I change microcontroller with more memory.
	I say 24+ bit number becouse I have used a seperate Byte for negative flags.
	This gives a number range of: -16,777,215 to 16,777,215.
	To make it more universal, all values are Ticks of the Motors Quadratic Encoder.

	Wire_Request converts as follows:

	Flags	(2 bytes Used to hold 16 single bit values like negative switches and flags)

		Slave_Buffer_Tx[0] and Slave_Buffer_Tx[1]
		Hold Flags

		Flags_1 true if:
			LSB		1	=	0x01 	Is_400K (default = 100K)
					2	=	0x02	Has_Station_A
					4	=	0x04	Has_Station_B
					8	=	0x08
					16	=	0x10
					32	=	0x20
					64	=	0x40
			MSB		128	=	0x80

		Flags_2 true if:
			LSB		1	=	0x01
					2	=	0x02
					4	=	0x04
					8	=	0x08
					16	=	0x10
					32	=	0x20
					64	=	0x40
			MSB		128	=	0x80

		Current positions (signed 32 bit, 4 bytes)
		Slave_Buffer_Tx[2] = CurPosition_A
		Slave_Buffer_Tx[6] = CurPosition_B

		I2C Address (unsigned 8 bit, 1 bytes)
		Slave_Buffer_Tx[10] = Requested_I2C_Address

		Stations (signed 16 bit, 2 bytes)
		Slave_Buffer_Tx[11] = Station_F_A
		Slave_Buffer_Tx[13] = Station_F_B
		Slave_Buffer_Tx[15] = Station_R_A
		Slave_Buffer_Tx[17] = Station_R_B

		Motor Loads (unsigned 16 bit. 2 bytes)
		Slave_Buffer_Tx[19] = _Val_A
		Slave_Buffer_Tx[21] = _Val_B


	The buffer holds 32 bytes, the rest are not used.
		Currently hold data version an maker.

Below is just for me to use as I use Visual Studio 2022 Comunity to edit code.
#include <Tims_Arduino_NANO.h>
*/

/*	Debug	*/
//#define DEBUG
#define SERIAL_PRINT

/*	Use ADC to read Motor Loads	*/
//#define USE_ADC

/*	Arduino IDE	*/
#include <Wire.h>
#include <LiquidCrystal_I2C.h>

/*	LCD	*/
LiquidCrystal_I2C lcd(0x27, 16, 2);

//#define TARGET_I2C_ADDRESS	0x30    /*  0x30=48 0x60=96 0x32=50Target Address.	*/
int Target_I2C_Address = 0x30;

#define BUFF_64				64      /*  What is the longest message Arduino can store?	*/
#define BUFF_16				16
#define BUFF_24				24
#define BUFF_32				32

#define SDA_PIN 4
#define SCL_PIN 5
const int16_t I2C_MASTER = 0x42;
const int16_t I2C_SLAVE = 0x08;

/*	SERIAL MESSAGES	*/
char Buffer_TX[BUFF_64];		/* message				*/
uint8_t Buffer_RX[BUFF_32];		/* message				*/
unsigned int no_data = 0;
unsigned int sofar;				/* size of Buffer_TX	*/
bool isComment = false;
bool procsessingString = false;
short cmd = -1;
bool slaveProcesing = false;
bool ProcsessingCommand = false;

/*	Debug	*/
long TimeNow = millis();
long Period = 1000;
long TimeOut = TimeNow + Period;

void setup() {
	/*
	  Start serial.
	*/
	Serial.begin(115200);
	/*
	  Start Wire.
		  Used only as Master atm. (address optional for master)
		  Wire.begin(SDA Pin, SCL Pin, Master Address);
	*/
	Wire.begin();
	Wire.setClock(400000);
	Wire.onRequest(Wire_Request);

	/*	LCD	*/
	lcd.init();
	lcd.backlight();
	lcd.print("   Tim's Dual   ");
	lcd.setCursor(0, 1);//bottom line
	lcd.print("  Motor Driver  ");



	/*	Debug	*/
	pinMode(LED_BUILTIN, OUTPUT);

}

void loop() {
	/*
		Tick - Tock
	*/
	TimeNow = millis();
	/*
		Get next command when finish current command.
	*/
	if (!procsessingString) { ReadSerial(); }

	if (TimeNow > TimeOut) {
		TimeOut = TimeNow + Period;
		digitalWrite(LED_BUILTIN, !digitalRead(LED_BUILTIN));
	}

}
/*
	Read Data in Serial Buffer if available.
*/
void ReadSerial() {
	if (Serial.available() > 0) {
		char c = Serial.read();
		no_data = 0;

		/*	Handle comments (G-code style)	*/
		if (c == '(' || c == ';') {
			isComment = true;
		}
		if (!isComment) {
			Buffer_TX[sofar++] = c;
		}
		if (c == ')') {
			isComment = false;
		}

		/*	Check for CRLF sequence	*/
		if (c == '\r') {
			delay(10);	/*	Short delay to allow LF to arrive	*/
			if (Serial.peek() == '\n') {
				Buffer_TX[sofar++] = Serial.read();	/*	consume LF	*/
				if (Serial.peek() == '\n'){
					Serial.read();	/*	consume extra LF	*/
				}

				/*	End of command detected	*/

				procsessingString = true;
				processCommand();
				init_process_string();
			}
		}
	}
}
/*
	Set ready for next command.
*/
void init_process_string() {

	memset(Buffer_TX, 0, BUFF_64);	/*	Clear transmit buffer	*/

	/*	Reset state variables	*/
	sofar = 0;
	procsessingString = false;
	isComment = false;
	cmd = -1;

	Serial.println("ok");	/*	Acknowledge ready for next command	*/

	/*	No flush or delay needed	*/

}
/*
	Change command numbers to a long.
*/
long Parse_Number(char code, long val) {
	/*
		start at the beginning of Buffer_TX.
	*/
	char* ptr = Buffer_TX;

	/*
	  Go char to char through string.
	*/
	while ((long)ptr > 1 && (*ptr) && (long)ptr < (long)Buffer_TX + sofar) {
		/*
			if you find code as you go through string.
		*/
		if (*ptr == code) {
			/*
				convert the digits that follow into a long and return it.
			*/
			return atol(ptr + 1);
		}
		/*
			take a step from here to the next char after the next space.
		*/
		ptr = strchr(ptr, ' ') + 1;
	}
	/*
		If the end is reached and nothing found, return val.
	*/
	return val;
}
/*
	Process Commands.
*/
void processCommand() {
	int32_t val32 = 0;
	int16_t val16 = 0;

	/*	Get I2C Address if given (default 0x30 or last sent)	*/
	Target_I2C_Address = Parse_Number('D', Target_I2C_Address);

	char* ptr = Buffer_TX;

	if (*ptr == 'X') {

#ifdef SERIAL_PRINT
		Serial.print("Buffer_TX ");
		Serial.print(Buffer_TX);
		Serial.print("   (");
		Serial.print(sofar);
		Serial.println(")");
		delay(50);
#endif  /*	SERIAL_PRINT	*/

		/*
			GET
				X					= gets all status info from the Motor Driver.
				X<number of bytes>	= gets number of bytes specified from the Motor Driver.
		
				Best values are:
					8	bytes		= Current Position A, Current Position B.
					9	bytes		= As above + I2C Address + I2C Speed.
					17	bytes		= As above + Station A and B info.
		
		*/
		int _numberOfBytes = Parse_Number('X', -1);
		if (_numberOfBytes == 0) _numberOfBytes = BUFF_32;

		/*	Clear RX buffer	*/
		for (size_t i = 0; i < BUFF_32; i++) Buffer_RX[i] = 0;

		Wire.requestFrom(Target_I2C_Address, _numberOfBytes);
		delayMicroseconds(10);

		for (size_t i = 0; i < _numberOfBytes && Wire.available(); i++) {
			Buffer_RX[i] = Wire.read();
		}

		/*	I2C Address check	*/
		if (Buffer_RX[10] == 0) {+
			Serial.println();
			Serial.print("No Address ");
			Serial.print(Target_I2C_Address, DEC);
			Serial.print(" (0x");
			Serial.print(Target_I2C_Address, HEX);
			Serial.println(") found.");
		}
		else {

			/*	Current Position A (int32)	*/
			val32 = (int32_t)Buffer_RX[2] |
				((int32_t)Buffer_RX[3] << 8) |
				((int32_t)Buffer_RX[4] << 16) |
				((int32_t)Buffer_RX[5] << 24);
			Serial.print("Current Position A = ");
			Serial.println(val32);

			/*	Current Position B (int32)	*/
			val32 = (int32_t)Buffer_RX[6] |
				((int32_t)Buffer_RX[7] << 8) |
				((int32_t)Buffer_RX[8] << 16) |
				((int32_t)Buffer_RX[9] << 24);
			Serial.print("Current Position B = ");
			Serial.println(val32);

			Serial.println();	/*	Add a Space	*/

			/*	I2C Address	*/
			Serial.print("I2C Address = ");
			Serial.print(Buffer_RX[10], DEC);
			Serial.print(" (0x");
			Serial.print(Buffer_RX[10], HEX);
			Serial.println(")");

			/*	I2C Speed	*/
			Serial.print("I2C Speed = ");
			Serial.println((Buffer_RX[0] & 0x01) ? "400000" : "100000");

			Serial.println();	/*	Add a Space	*/

			/*	Station A ON/OFF	*/
			Serial.print("Station A = ");
			Serial.println((Buffer_RX[0] & 0x02) ? "ON" : "OFF");

			/*	Station Forward A (int8)	*/
			val16 = (int8_t)Buffer_RX[11];
			Serial.print("Station A Forward = ");
			Serial.println(val16);

			/*	Station Reverse A (int8)	*/
			val16 = (int8_t)Buffer_RX[12];
			Serial.print("Station A Reverse = ");
			Serial.println(val16);

			/*	Acceleration A Rate (unsigned 16 bit)	*/
			val16 = (Buffer_RX[24] << 8) | Buffer_RX[23];
			Serial.print("Acceleration A = ");
			Serial.println(val16);

			/*	Encoder Slot Count (unsigned 16 bit)	*/
			val16 = (Buffer_RX[28] << 8) | Buffer_RX[27];
			Serial.print("Encoder A Slot Count = ");
			Serial.println(val16);

			Serial.println();	/*	Add a Space	*/

			/*	Station B ON/OFF	*/
			Serial.print("Station B = ");
			Serial.println((Buffer_RX[0] & 0x04) ? "ON" : "OFF");

			/*	Station Forward B (int8)	*/
			val16 = (int8_t)Buffer_RX[13];
			Serial.print("Station B Forward = ");
			Serial.println(val16);

			/*	Station Reverse B (int8)	*/
			val16 = (int8_t)Buffer_RX[14];
			Serial.print("Station B Reverse = ");
			Serial.println(val16);

			/*	Acceleration B Rate (unsigned 16 bit)	*/
			val16 = (Buffer_RX[26] << 8) | Buffer_RX[25];
			Serial.print("Acceleration B = ");
			Serial.println(val16);

			/*	Encoder B Slot Count (unsigned 16 bit)	*/
			val16 = (Buffer_RX[30] << 8) | Buffer_RX[29];
			Serial.print("Encoder Slot Count B = ");
			Serial.println(val16);

			Serial.println();	/*	Add a Space	*/

#ifdef USE_ADC
			/*	Motor Load A (uint16)	*/
			val16 = (Buffer_RX[20] << 8) | Buffer_RX[19];
			Serial.print("Motor Load A = ");
			Serial.println(val16);

			/*	Motor Load B (uint16)	*/
			val16 = (Buffer_RX[22] << 8) | Buffer_RX[21];
			Serial.print("Motor Load B = ");
			Serial.println(val16);

			Serial.println();	/*	Add a Space	*/
#endif

			Serial.println("Tim");
		}
	}
	else if (*ptr == 'P') {
		/*	Process command (future expansion)	*/
	}
	else {
		/*	SEND	*/
		ProcsessingCommand = true;
		SendBufferOnI2C(Target_I2C_Address);
		delay(4);
		ProcsessingCommand = false;
	}
}
/*
	Send Recived Commands on to a Device on the I2C bus.
*/
void SendBufferOnI2C(int I2C_address) {

	Wire.beginTransmission(I2C_address);	//	Get device at I2C_address attention
	Wire.write('#');						/*	Send garbage for the first byte of data that will be ignored.	*/
	Wire.write(Buffer_TX, sofar);			//	Send Buffer_TX
	Wire.endTransmission();					//	Stop transmitting

#ifdef SERIAL_PRINT
	Serial.print("Buffer_TX ");
	Serial.print(Buffer_TX);
	Serial.print("   (");
	Serial.print(sofar);
	Serial.println(")");
	delay(50);
#endif  /*	SERIAL_PRINT	*/

}
/*
	I2C Request Data
*/
void Wire_Request() {

}

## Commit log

2024-09-30 Add project files.
    [Tims_I2C_Dual_Motor_Driver_V2.csv, Tims_I2C_Dual_Motor_Driver_V2.kicad_pcb, Tims_I2C_Dual_Motor_Driver_V2.kicad_sch]
2025-11-24 Update web
    [Tims_I2C_Dual_Motor_Driver_V2.FCStd, Tims_I2C_Dual_Motor_Driver_V2.csv, Tims_I2C_Dual_Motor_Driver_V2.kicad_pcb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]
2025-11-24 Added Version 3 Firmware for Version 2 PCB,
